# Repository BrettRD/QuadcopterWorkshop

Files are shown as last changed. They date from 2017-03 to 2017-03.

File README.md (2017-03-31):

# QuadcopterWorkshop
An intro to quadcopters workshop developed with Protospace

This repo contains a frame designed for laser-cutting from 4mm ply.

## Assembly
This frame only has four bolts to hold it together, and various parts are held in place by the frame geometry.
Once assembled, the frame is reasonably sturdy, but you may need an additional pair of arms to assemble it.

### Prep the parts
Some of the components need soldering before they can be used
* The motors need 3.5mm bullet connectors soldered to their fly-leads. Apply 10mm of 4.5mm heat-shrink.
* The flight controller needs headers soldered in place, and case screwed together.
* The ESCs and battery connector need to be soldered to the PDB - ESCs come off the PDB diagonals, positive leads front and rear, negative leads out the sides. One negative lead will share a place with the battery connector.
* The Props are designed to suit any motor shaft diameter up to 8mm and come with 8mm retainers, but require drilling out beyond 6mm.  Use a dull drill bit in a cordless drill to allow the bit to self-centre. (using a drill press requires extremely careful alignment)

### Order of assembly
I encourage you to skip ahead where possible, change things, refer to the example copy for details, and do your own thing.
This assembly order only applies for the frame design as supplied, and serves as notes for things that get hard when you do them the other way around.\
* Loop the battery strap through the base plate before fastening the PDB
* Fasten the PDB (with ESCs) to the the base plate with two layers of foam tape either side of the battery strap.
  Bolt holes are marked, but using foam tape leaves less hard points for the battery to snag on in a rough landing.
* Place the ESCs inside the arms. (Two outputs toward the straighter edge of the arm)
* Bolt the frame together with 4x M4 bolts (four to six hands recommended).
* Bolt the motors to the arms, paying attention to the direction of rotation (left and right hand thread on the prop adapter), cables draping over the straighter edge of the arms
* Fasten the flight controller using soft foam tape.
* Fasten the RC receiver to the base plate using foam tape.
* Plug the Naze32 RC lead into the receiver. Only pins 1-6 are important on this build.
* Plug the ESCs and receiver cable into the Naze32.
* Plug the flight controller into your laptop and configure it.
* Plug the motors into the ESCs. (if a motor spins the wrong way, swap two of its cables)
* Get someone to sanity-check your work before connecting the battery.

## Configuration
The flight controller and radio gear requires some basic set up.
### Receiver
Set the transmitter trim tabs to their mid points, and the throttle trim to minimum. (mid throttle trim is too high and prevents arming the copter.)
### Radio Binding
Modern radios permit multiple devices on the same frequency.  Plug the bind loop into the receiver and apply power, hold the bind button on the transmitter as you turn it on. The two devices should associate with each other. Power down everything and remove the bind loop. (make sure only one person tries this process at a time.)
### Axis inversions
The transmitter has four switches that allow you to invert any of its four axes. This build needs all but the Ailerons reversed.
### Flight Controller
The flight controller here is the NAZE32 Acro.  This controller runs the [Cleanflight](http://cleanflight.com/) software, which has its roots in the MultiWii code base. It is very popular as a reliable, no-nonsense racing controller.
You change the settings with the [Cleanflight Configurator](https://chrome.google.com/webstore/detail/cleanflight-configurator/enacoimjcgeinfnnnpajinjgmkahmfgb) Chromium App.
#### Flight modes
An auxiliary channel can be used to change flight behaviours. We lack such an auxiliary channel, so set all modes the same.  There are a few options to choose from, so I'll go over the important ones here:
* Rate gives you control over how quickly the copter rotates on its axes.  This is great for racing because it gives you a lot of control over the flight dynamics.  This mode requires the most attention
* Angle gives you control of the angle of the body. It won't let you flip over, but still offers good control.
* Horizon is a friendly mixed mode that will keep your copter level, but still allows you to roll all the way over when you really mean it.
* Baro takes control of the throttle, using the barometer as an altitude reference, and you tell it how fast to climb or descend.  This can lead to problems when you want to come down in a hurry, or the copter bounces endlessly on landing.
#### Motor calibration
All ESCs need to agree on minimum and maximum signals. You can do this all at once via the motors page. (remove the props)
Set the Master slider to maximum, then connect the battery.  Slide it to the bottom and back to the top twice, listening to the tunes.
After measuring minimum throttle twice, the motors will turn when you give them throttle via the sliders.

## Flight Issues

### Arming test
Move the throttle stick into the arming position (minimum throttle, full right yaw), and watch the green LED in the Naze32. if it goes from blinking to solid, you're ready to fly.
Move the throttle stick into the disarm position (minimum throttle, full left yaw), and the greem LED should turn off.

### Arming Problems
* Check your receiver is bound, (the LED on the receiver shoudld be lit only when the transmitter is on)
* On the handset, the Rudder, Throttle and Elevator should be reversed.  Ailerons should be normal.
* Throttle trim should be set to minimum. (trims are the small sliders by each stick axis)
* Yaw trim should be set to zero (mid).

### Flip on takeoff
* check the props are rotating the correct directions, you can find this diagram in Cleanflight-Configurator when you connect the flight controller.
* If a motor is turning backwards, swap two of its wires at the ESC.

## Taking it further
These parts were chosen as a solid starting point for a hobby in RC aircraft.\
The flight controller is designed for racing copters, while the motors and ESCs are capable of lifting sensor packs and cameras.\
The transmitter was chosen to be appropriate as a "buddy box" or trainer handset alongside a more capable transmitter.\
To get into racing, you'll want to recude the total size, motor mass, and prop diameter.\
To get into autonomous platforms with advanced sensor packs, you'll want to swap the flight controller for something more advanced like the Pixhawk or Pixracer running the Ardupilot firmware.

## Glossary
* ESC: electrically switched commutator / electronic speed controller
* PDB: power distribution board

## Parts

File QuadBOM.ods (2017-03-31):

Flight Gear | Description | Vendor URL | packs per user | Notes
330 class frame | plywood, 4mm thick 300x600 | protospace | 1
Battery | 1.8Ah 3s xt60 | https://hobbyking.com/en_us/turnigy-1800mah-3s-40c-lipo-pack.html | 1 | select global warehouse
Handset | Hobbyking 4ch | https://hobbyking.com/en_us/hobby-king-2-4ghz-4ch-tx-rx-v2-mode-2.html | 1 | select global warehouse
Tx | Built-into HK handset | see above
Rx | Included w HK handset | see above
TX battery | 8x AA cells | protospace
Motors | D2212 with integrated prop adapter 4pack | https://www.aliexpress.com/item/F14711-A-4Pcs-CW-CCW-2212-920KV-Brushless-Motor-for-3-4S-RC-Quadcopter-DJI-Phantom/32371868989.html | 1
Props | 8045 2blade | https://www.aliexpress.com/item/Red-8045-8X4-5-20-Pair-EPP-Propeller-CW-CCW-Prop-for-DJI/1766661075.html | 0.2
ESCs | 30A Blheli white (integrated socket) | https://www.aliexpress.com/item/F18124-4-6-5-1-Set-JMT-30A-SimonK-Blheli-2-4S-Lipo-5V-3A-BEC/32684057916.html | 1 | 4 packs, Blheli firmware
BEC | integrated in ESC | see above | -
Flight Controller | Naze32 6Dof Acro | https://www.aliexpress.com/store/product/F17278-9-NAZE32-REV6-Full-Acro-Version-Flight-Controller-Board-with-Case-for-DIY-Drone-FPV/100989_32635679212.html | 1
Power distribution board | basic PCB only | https://www.aliexpress.com/item/Niosung-Multirotor-ESC-Power-Distribution-Battery-Board-For-Quadcopter-Multi-Axis-Model/32729244956.html | 10
silicone cable | PDB-battery flylead | https://www.aliexpress.com/item/1meter-Red-1meter-Black-12-12-AWG-12AWG-Heatproof-Soft-Silicone-Silica-Gel-Wire-Connect-Cable/32776787452.html | 0.1
XT60 connector | 10 pairs | https://www.aliexpress.com/item/20pcs-XT60-XT-60-Male-Female-Bullet-Connectors-Plugs-For-RC-Lipo-Battery-10-pair-Wholesale/32665512004.html | 0.1
Lipo Charger | basic charger | https://www.aliexpress.com/item/Wholesale-Balancer-Charger-Balance-Charger-For-7-4-11-V-2-3S-2S-3S-Cells-Li/32707115132.html | 1
Motor connectors | Connectors 3.5mm bullet | https://www.aliexpress.com/store/product/F00149-6-6Pairs-Thick-Gold-Plated-3-5mm-Bullet-Connector-banana-plug-for-ESC-battery/100989_32646793467.html | 2
zip ties |  | protospace
foam tape | soft, open-cell foam adhesive both sides | protospace
velcro straps | 10mm wide, 200mm long | protospace
Motor Bolts | M3 x 6mm bolts, 16 per user | protospace

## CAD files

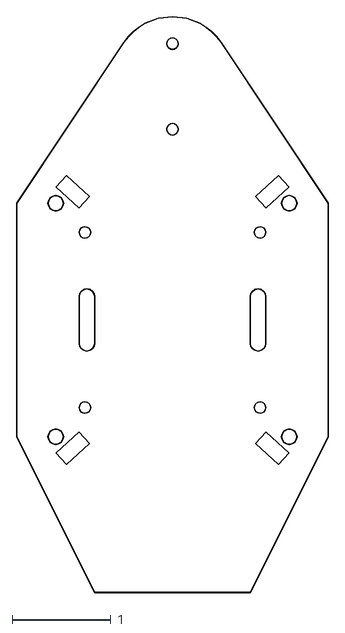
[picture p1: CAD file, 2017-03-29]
Customisations/Minimal330gpsBaseplate.dxf
3.16 x 5.84

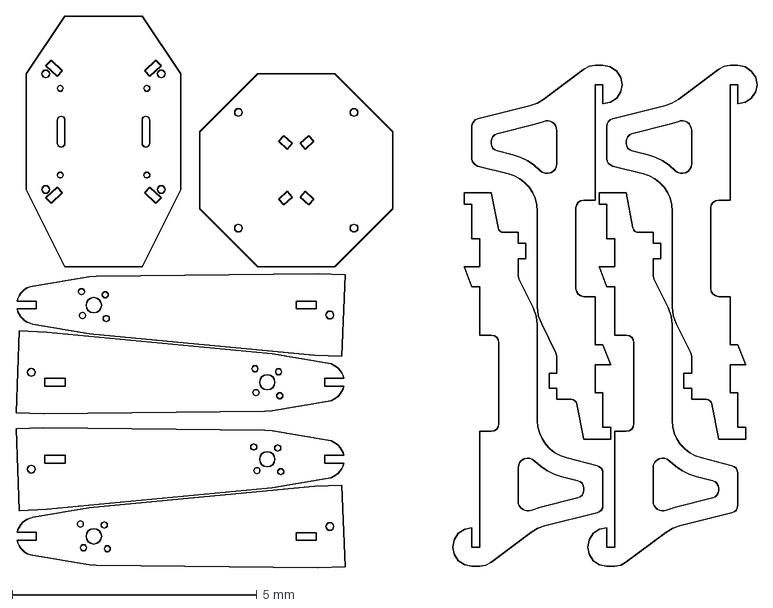
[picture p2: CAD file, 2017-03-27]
Minimal330Panels.dxf
15.1 x 11.3 mm

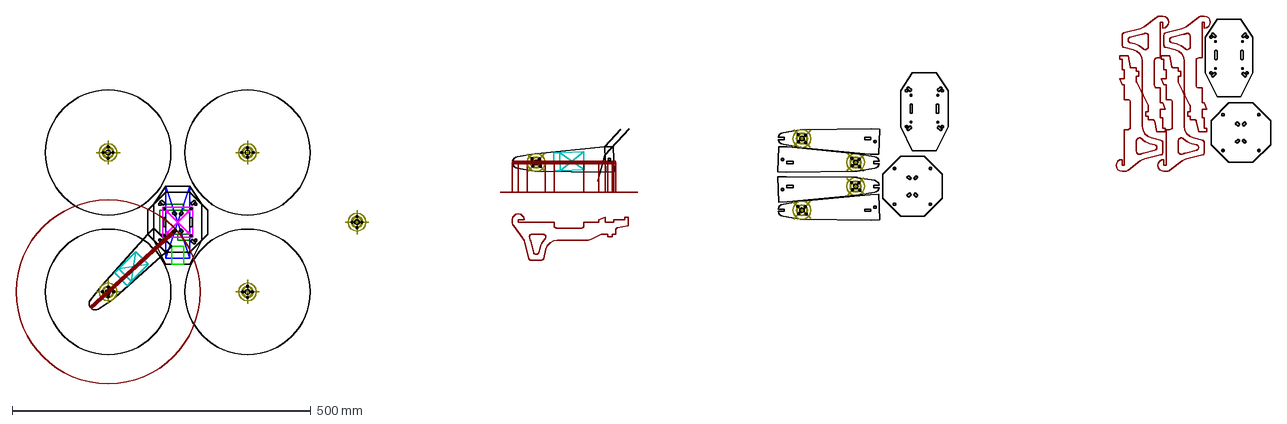
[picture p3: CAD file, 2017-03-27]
Minimal330.dxf
2100.6 x 615.6 mm

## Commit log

2017-03-27 330 class frame after flight tests
    [Minimal330.dxf, Minimal330Panels.dxf]
2017-03-27 cleaned geometry lines
    [Minimal330Panels.dxf]
2017-03-29 added baseplate file with GPS
    [Minimal330gpsBaseplate.dxf]
2017-03-31 added BOM
    [Minimal330gpsBaseplate.dxf, QuadBOM.ods]
